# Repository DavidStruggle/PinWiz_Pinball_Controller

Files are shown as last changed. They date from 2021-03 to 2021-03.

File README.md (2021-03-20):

# PinWiz Pinball Controller
 ~ Purpuse Build Open Source Pinball Controller ~ 

## Features
- 10×10 Lamp driver Matrix ( LED and incandescent possible)
- 10×10 Switch matrix
- 40 High Power drivers
- 2.1ch Audio Amplifier  (2x 19W + 1x50W)
- 2ch General Illumination
- 2 Stepper Motor Drivers

## TODO
- Clean up schematics
- Include detailed BOM

## Background
I know that there are other “DIY” Pinball controllers like the PROC or the OPP, but I wanted to do my own (focused on fitting my pinball project). A big difference between my board and these boards is that i am using a central processor for doing everything rather than decentral boards, which do have their own processing unit on them. 

### Extract from my Blog
#### Audio Amplifier

The original game uses stereo music files and mono sound effects (sometimes panned to one speaker).  We also have a woofer in the cabinet, so it would make sense to have a tree way amplifier: two channels for the speakers, one for the woofer. Texas Instruments offers an IC, that fulfills our requirements. The TAS5755M is a very cool and relatively cheap chip. It is controlled by I2C and gets the sound data over standard I2S. I2S is very interesting, since we are basically sending a PCM signal to the codec. PCM is an uncompressed audio format found in wav files, which we are already have from the game files (more on that later). So we just need to read that file and send that exact data over to the codec without decompressing. This saves a lot of CPU load. Mixing multiple files is also easy since we can use simple addition (..and in some cases multiplication/division).

Another Bonus is, that the codec has an internal equalizer, which we can use to get the maximum sound quality out of our cabinet (..and adding a low pass filter to the subwoofer).

##### Stepper Motor Driver

Driving stepper motors is pretty straight forward: All you need are two H-Bridges and you are set (for an bipolar stepper motor). However, this will take some CPU load, handling the PWM signals to the bridges. While investigating, I found an interesting IC. The PCA9629A from NXP can control an uni polar stepper motor (with the help of some external components) over I2C. It has many features like ramping up and down, going x steps, reacting to interrupts and GPIO states. With the help of this IC, we can minimize another load on our processor. I also find it neat to see, that the datasheets states Amusement Machines as the first suggested use case 🙂

#### Solenoid drivers

There is not much to say for this one: The Solenoids will be fired by controlling an IRL540N mosfet in open drain configuration (it pulls the solenoid to ground). The mosfet is driven by a SN74ABT2827 buffer, which has multiple use cases: it is used as an watchdog, disabling all solenoids if the microprocessor has any problem, it is used to safe the microprocessor in case the mosfet fails and it is used as an level translator, since the microprocessor runs at 3.3v and the mosfet likes a gate-source voltage of around 5V.

#### Lamp Matrix drivers

Basically this is a standard TIP102 / TIP107 configuration as you see it on most pinball machines. The TIP102 NPN are buffered with a SN74ABT2827 and the TIP107 PNP are pulled low by ULN2003A darlington arrays. 

#### Switch Matrix drivers
The most simple solution yet: Just In/Out Buffers (SN74ABT2827) controlled by the microcontroller.

#### General Illumination
An IRL540N mosfet driven by a MCP1402 gate driver (used again as level translator). This mosfet will be PWM controlled. 

#### The Microcontroller
The heart of our machine. I have very pleasant experience with the STM32 series of microcontrollers so I stuck with them. The biggest factors here for choosing a microcontroller are:

    Amount of GPIOs
    I2S
    I2C
    SDIO (..at least SPI)
    SPI 

There are quite a few microcontrollers which fulfill our criteria. Luckily, most of them pin compatible. Candidates are : STM32F469 (IE, II or IG) STM32F767 (II or IG), or even STM32H743 (II or IG).

I chose the STM32F767 – it should be more than enough powerful for what we will use it. You could however choose another controller if you like. Porting the source code should not be a problem, since they are all backwards compatible.

#### Miscellaneous

An SD card is directly connected to the microcontroller. The DMD will also be driven directly from the microcontroller. A backup SRAM battery has been added to store variables in SRAM and keep time and date. I probably wont end up using the SRAM for high scores, statistics and options, since its volitale. These things will probably end up in Flash or on the SD (which should be fine, since they are not written all the time). The microcontroller will be programmable over JTAG or SWD. In this case, I have gone with SWD, since it works great on the Nucleo boards.

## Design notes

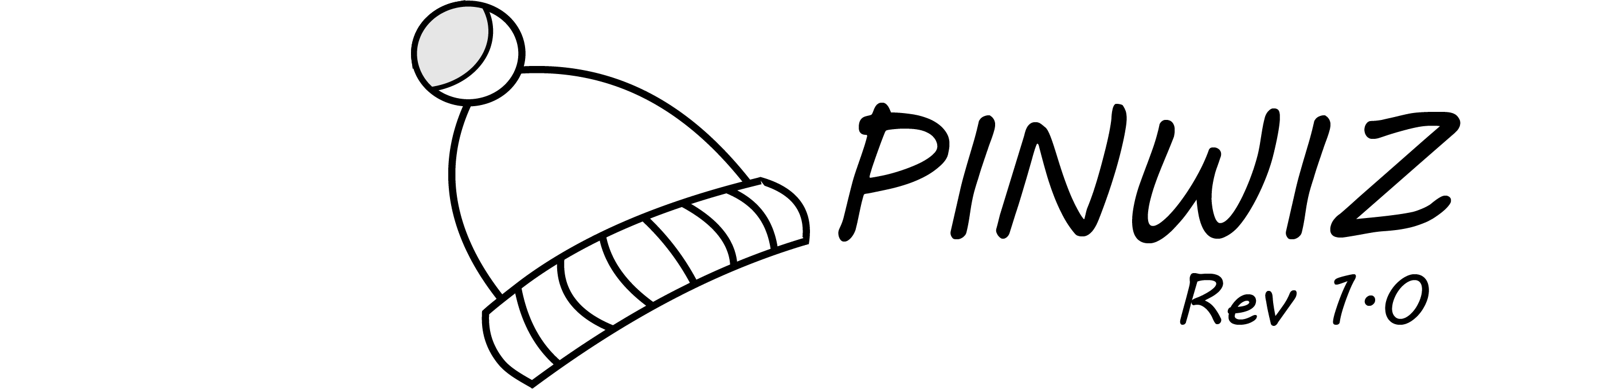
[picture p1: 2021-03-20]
Graphics/PinWiz.png

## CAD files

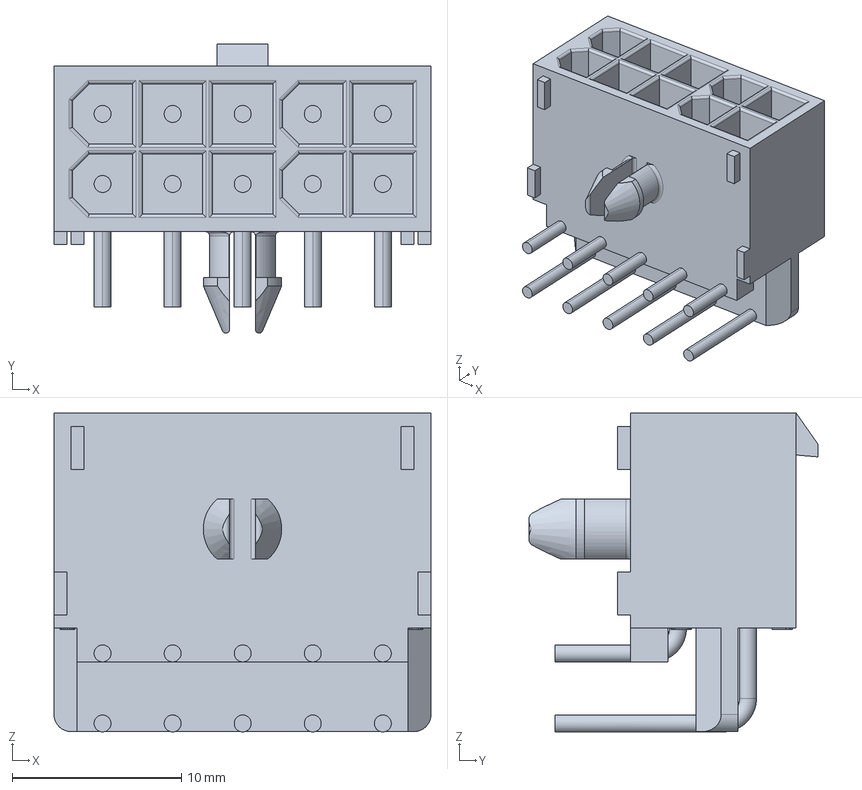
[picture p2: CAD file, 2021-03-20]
Design Files/3D_Modelle/c-770971-1-e-3d.stp
22.3 x 17.1 x 18.8 mm

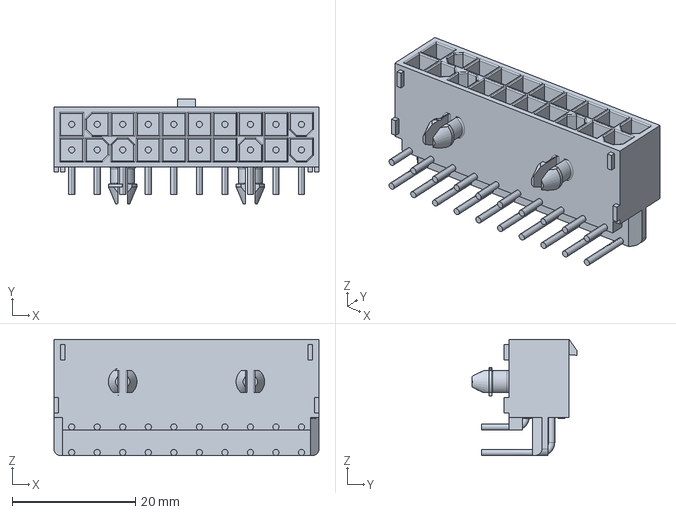
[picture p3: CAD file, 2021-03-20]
Design Files/3D_Modelle/c-794106-2-b-3d.stp
43.0 x 17.1 x 18.8 mm

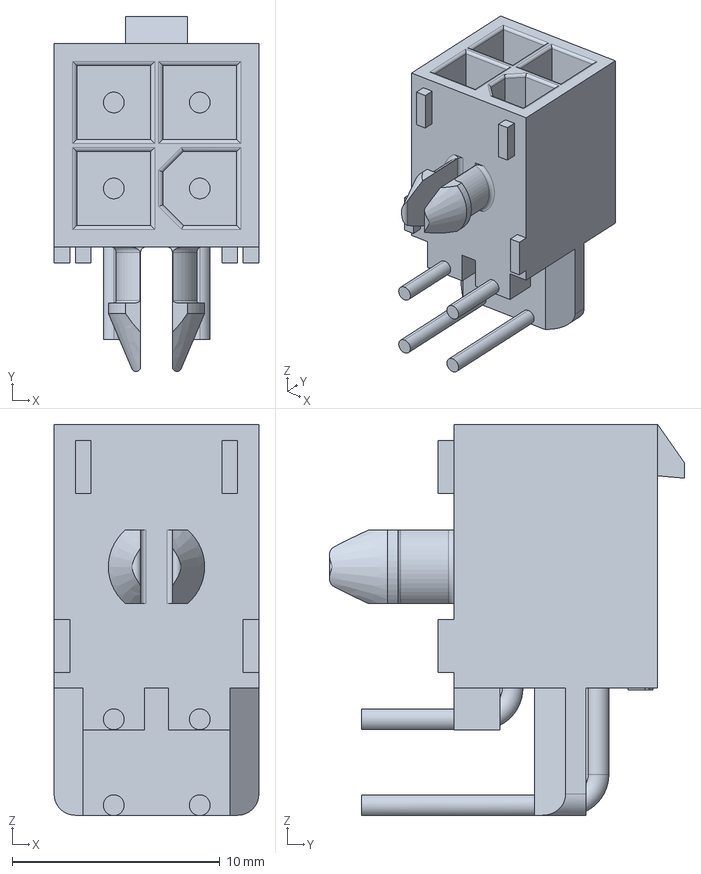
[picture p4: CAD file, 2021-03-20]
Design Files/3D_Modelle/c-1-770968-0-e-3d.stp
9.86 x 17.1 x 18.8 mm

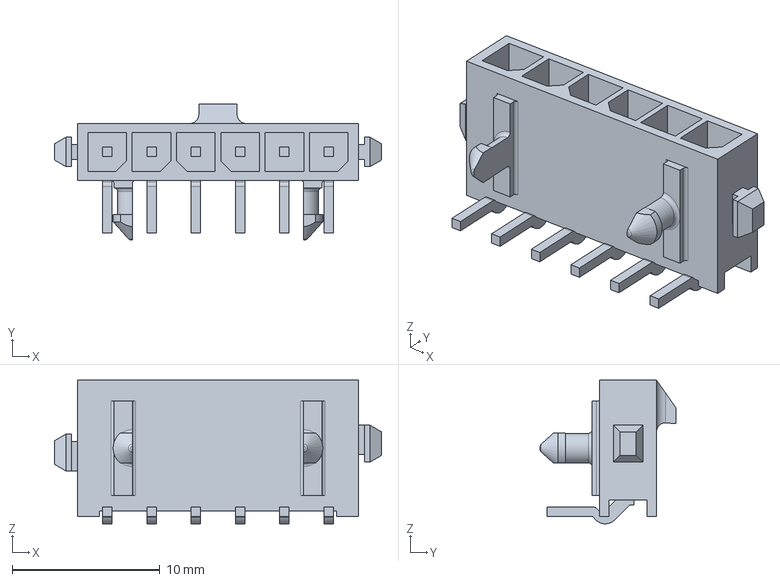
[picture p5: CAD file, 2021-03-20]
Design Files/3D_Modelle/c-1445098-6-b-3d.stp
22.1 x 9.18 x 9.73 mm

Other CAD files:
Graphics/PinWiz.dwg

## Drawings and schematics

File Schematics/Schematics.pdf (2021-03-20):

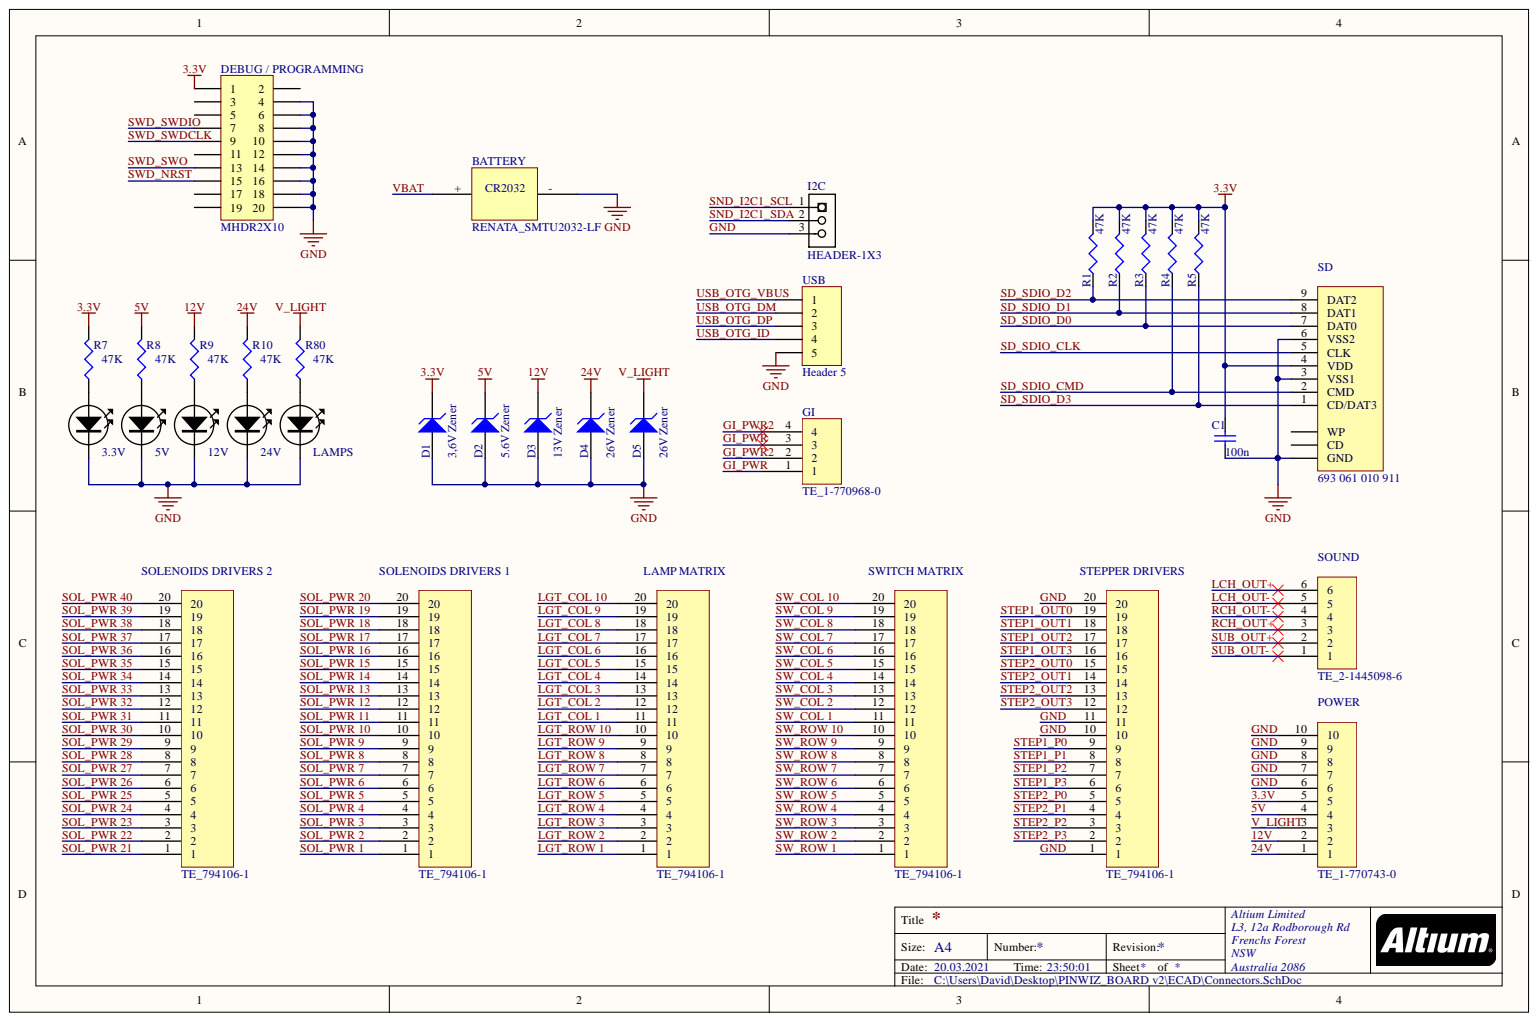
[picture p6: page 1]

* Title | Altium Limited L3, 12a Rodborough Rd Frenchs Forest NSW Australia 2086

A4 Size: | * Number: | * Revision:
Date: 20.03.2021 Time: 23:50:01 | | Sheet * of *

C:\Users\David\Desktop\PINWIZ_BOARD v2\ECAD\Connectors.SchDoc

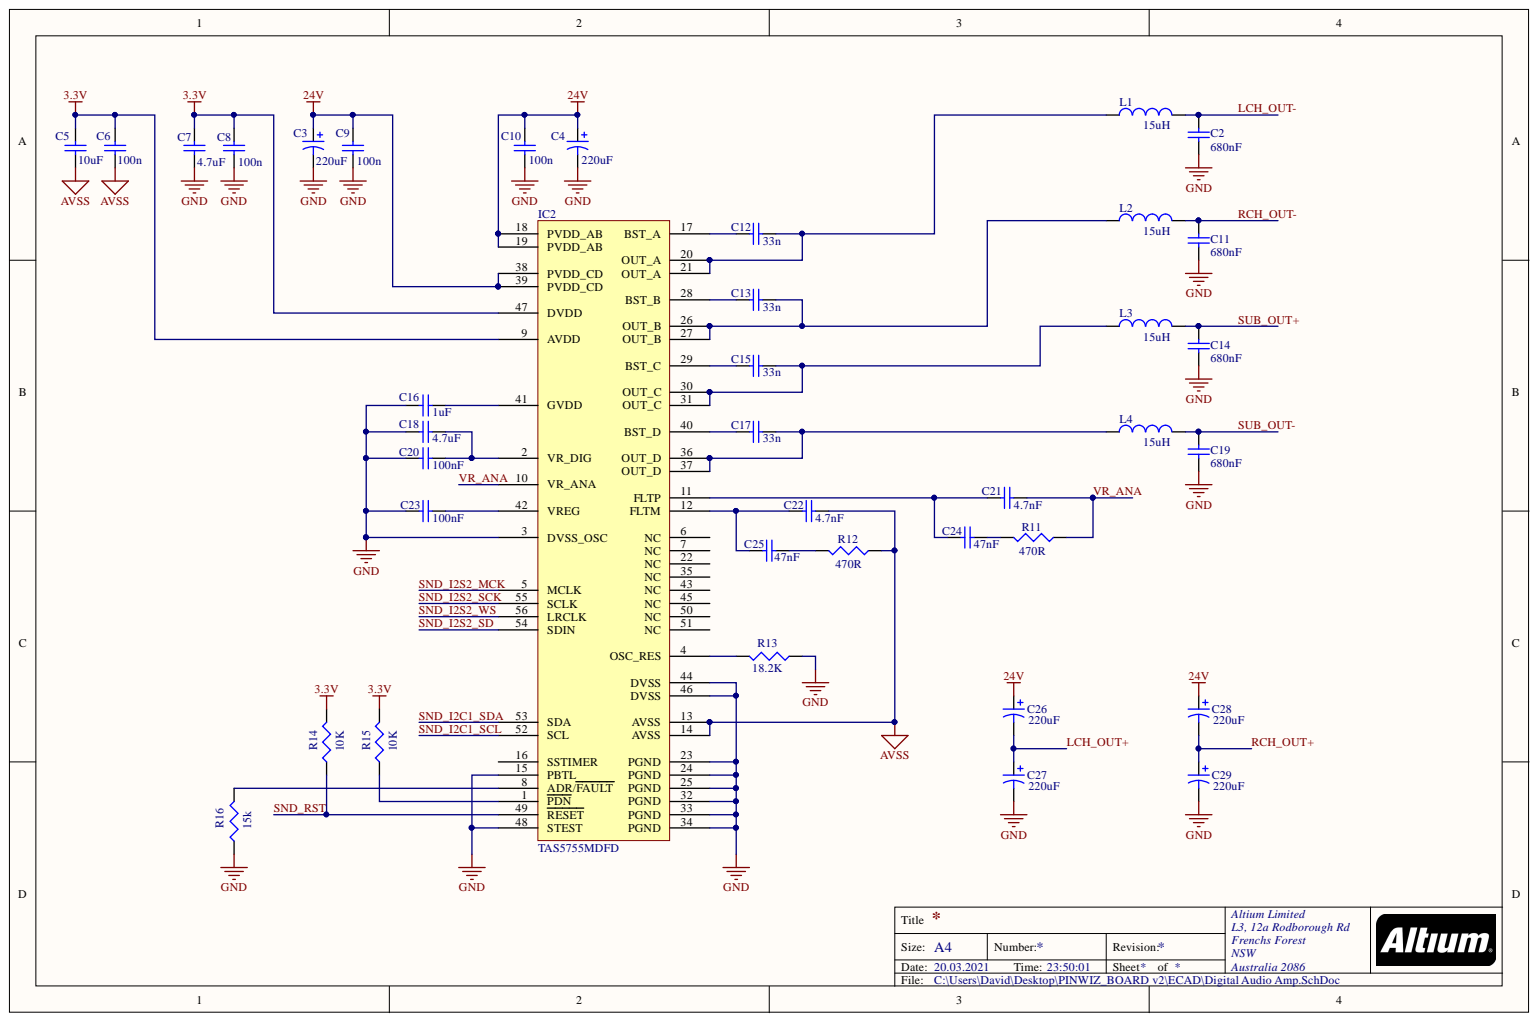
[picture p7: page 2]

8 | | 2 5
1 | | 3 2
4 9 | | 3 3
4 | | 3 4

* T i t l e | A l t i u m Li m i ted L3, 1 2 a R o d b o ro u g h R d F rench s F o res t NS W A u s t r a l i a 2

A4 Size: | * N umber: | * Rev i s i o n :

0.0 3.2 T ime: : : | | Sheet o f

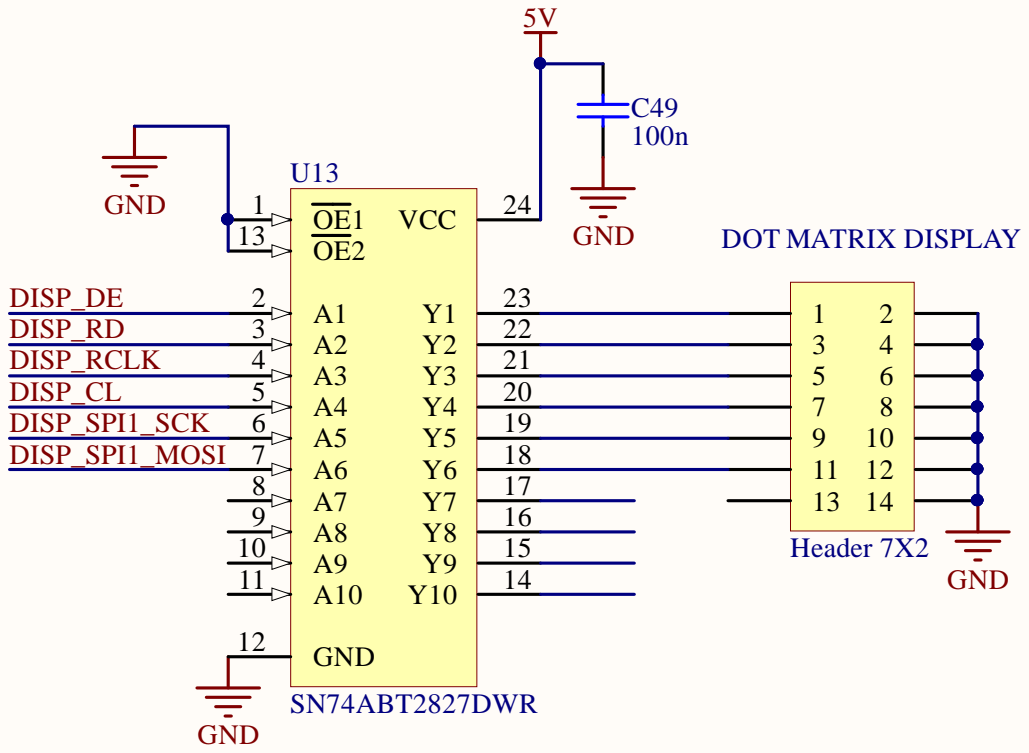
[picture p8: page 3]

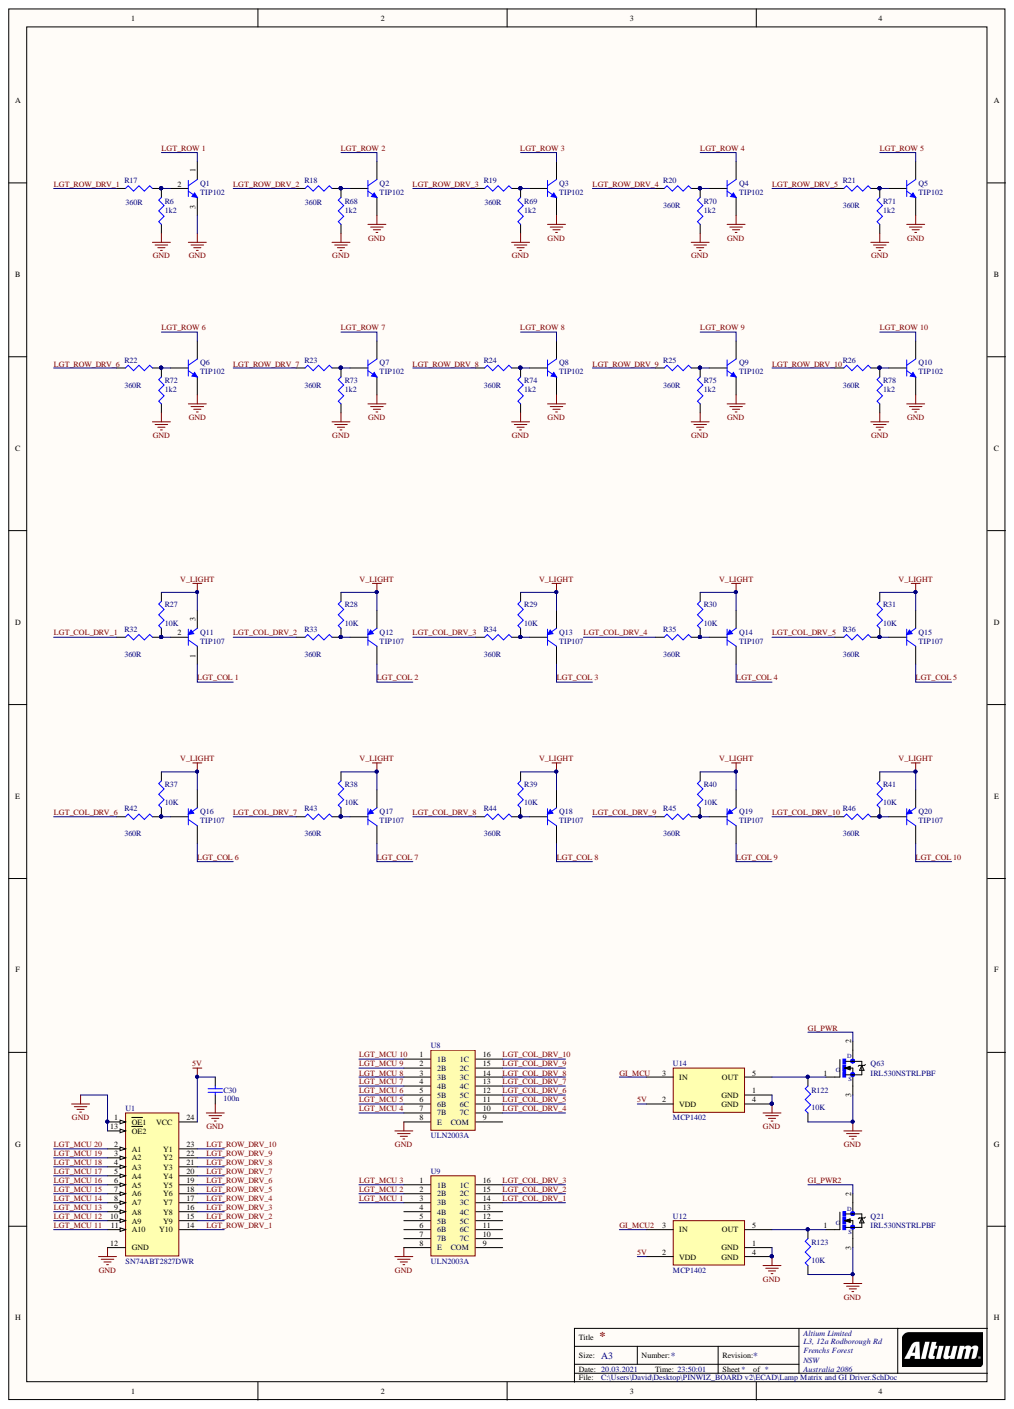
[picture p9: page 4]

Title | Altium Limited L3, 12a Rodborough Rd Frenchs Forest NSW

Size: A3 | Number: * | Revision: *

C:\Users\David\Desktop\PINWIZ_BOARD v2\ECAD\Lamp Matrix and GI Driver.SchDoc

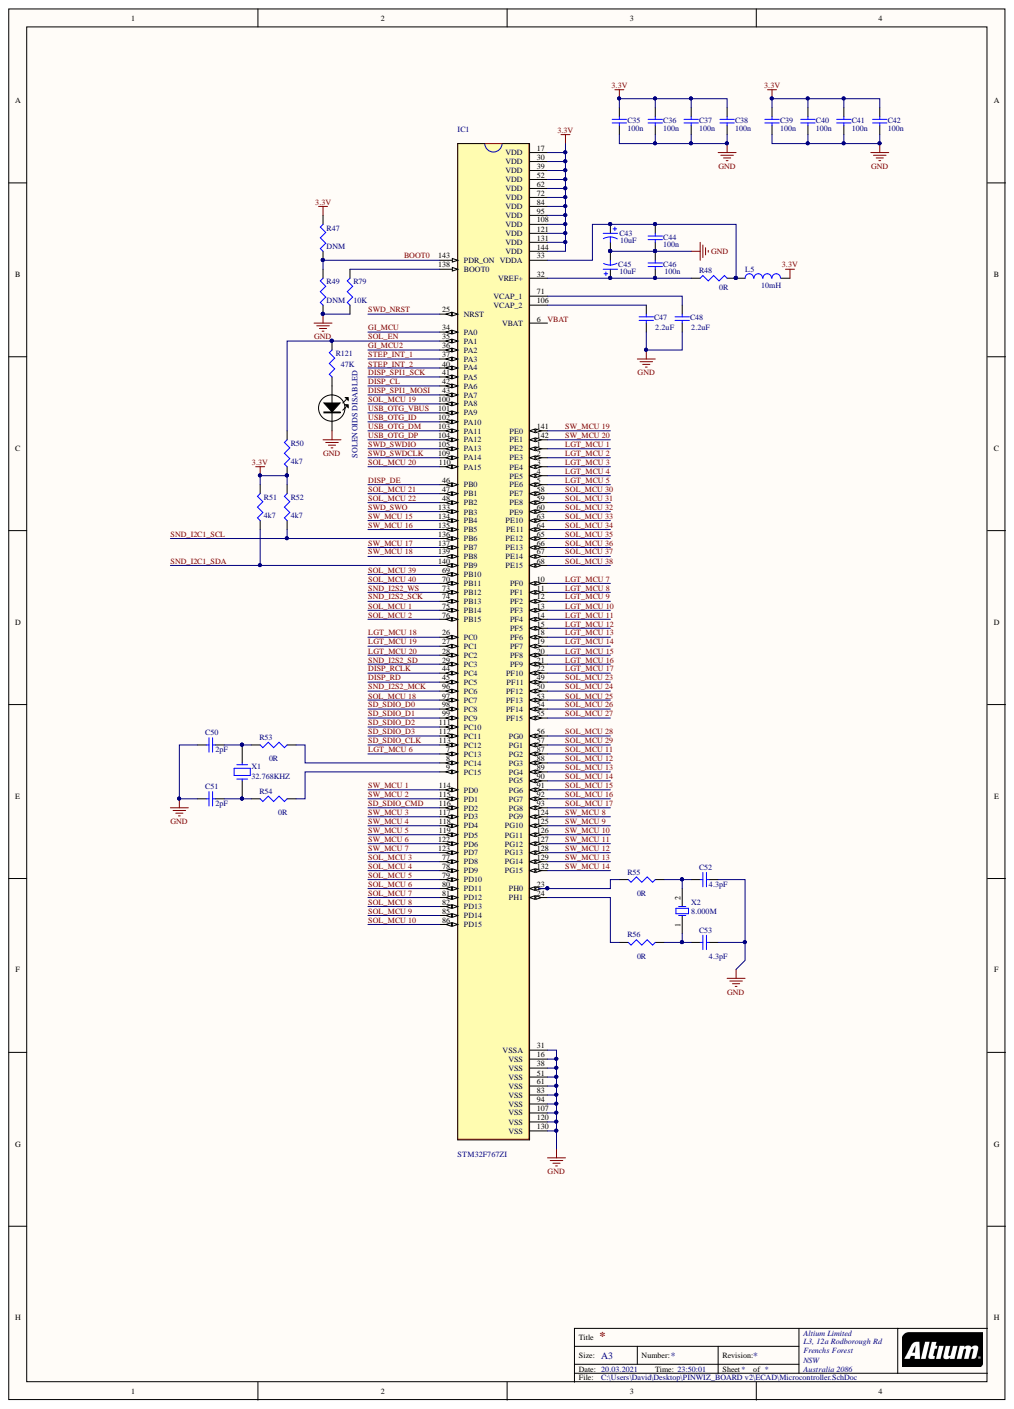
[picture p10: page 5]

Title | Altium Limited L3, 12a Rodborough Rd Frenchs Forest NSW

Size: A3 | Number: * | Revision: *

C:\Users\David\Desktop\PINWIZ_BOARD v2\ECAD\Microcontroller.SchDoc

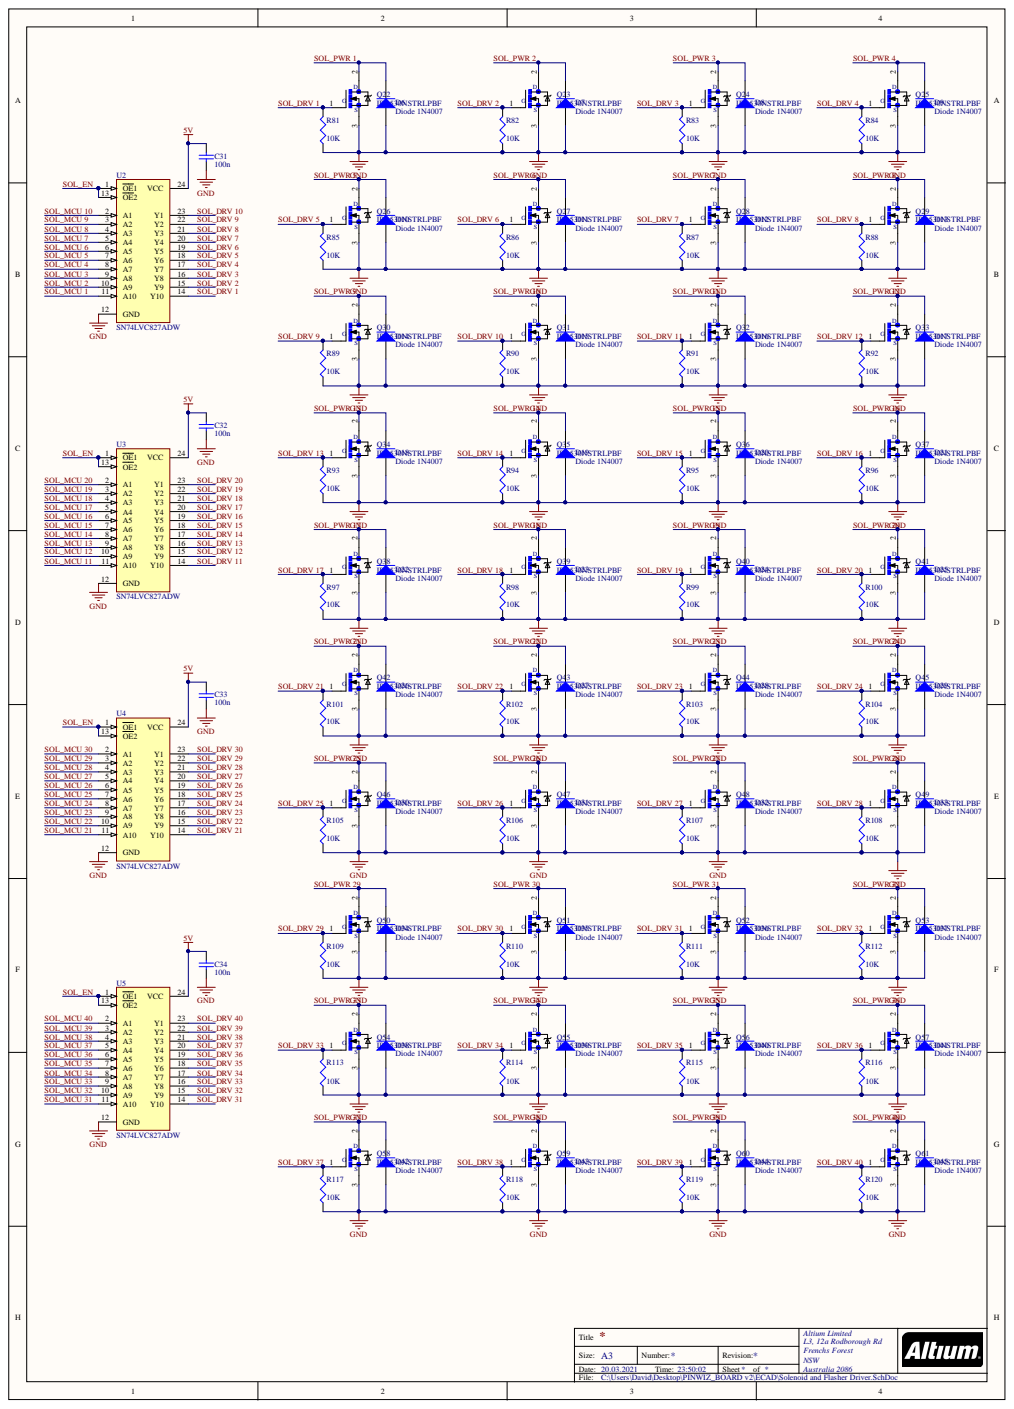
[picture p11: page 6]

Altium Limite d L3, 12a Rodborough R d F renchs Fore s t NSW Australia 2086

A | r : | R evision:

Date : Time : | | She e t of
File : Z_BOARD v2\E CAD\Solenoid and Fla she r Drive r . S chDoc

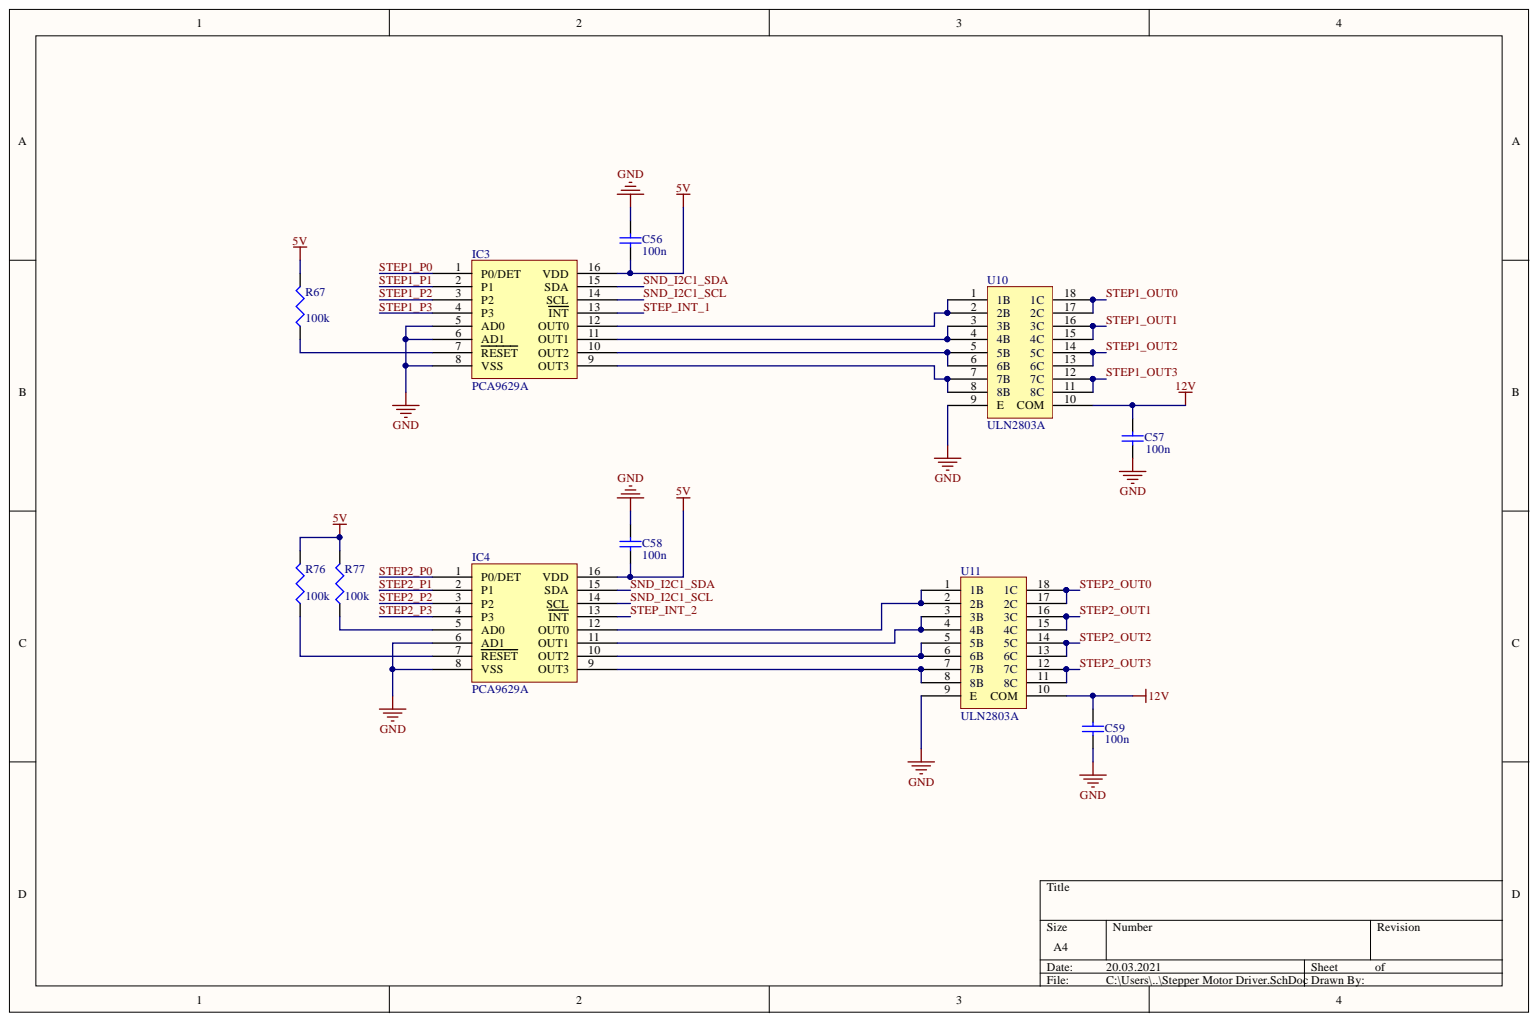
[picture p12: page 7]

6 | | 1 1 | | 4 | 1 5
7 | | 1 0 5

8 | 1 1

6 | | 1 1 | | 5
7 | | 1 0 | | 6 | 1 3

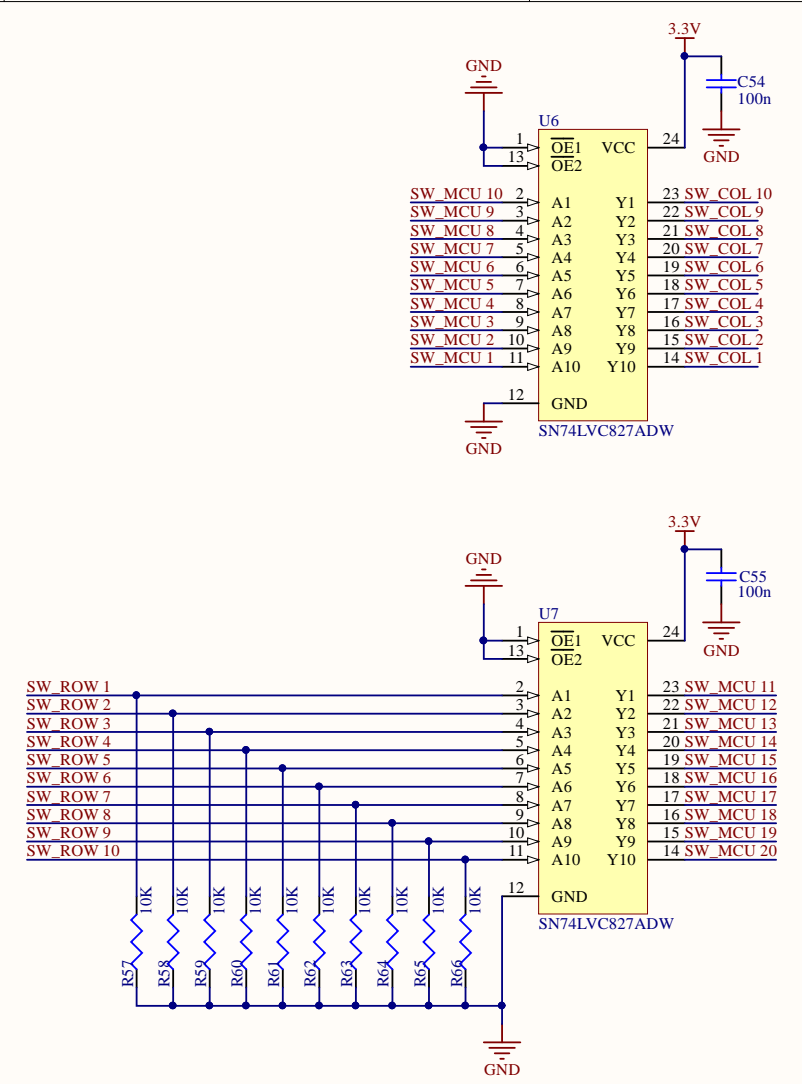
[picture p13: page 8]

* Title | Altium Limited L3, 12a Rodborough Rd Frenchs Forest NSW

A4 Size: | * Number: | * Revision:

C:\Users\David\Desktop\PINWIZ_BOARD v2\ECAD\Switch Matrix Driver.SchDoc

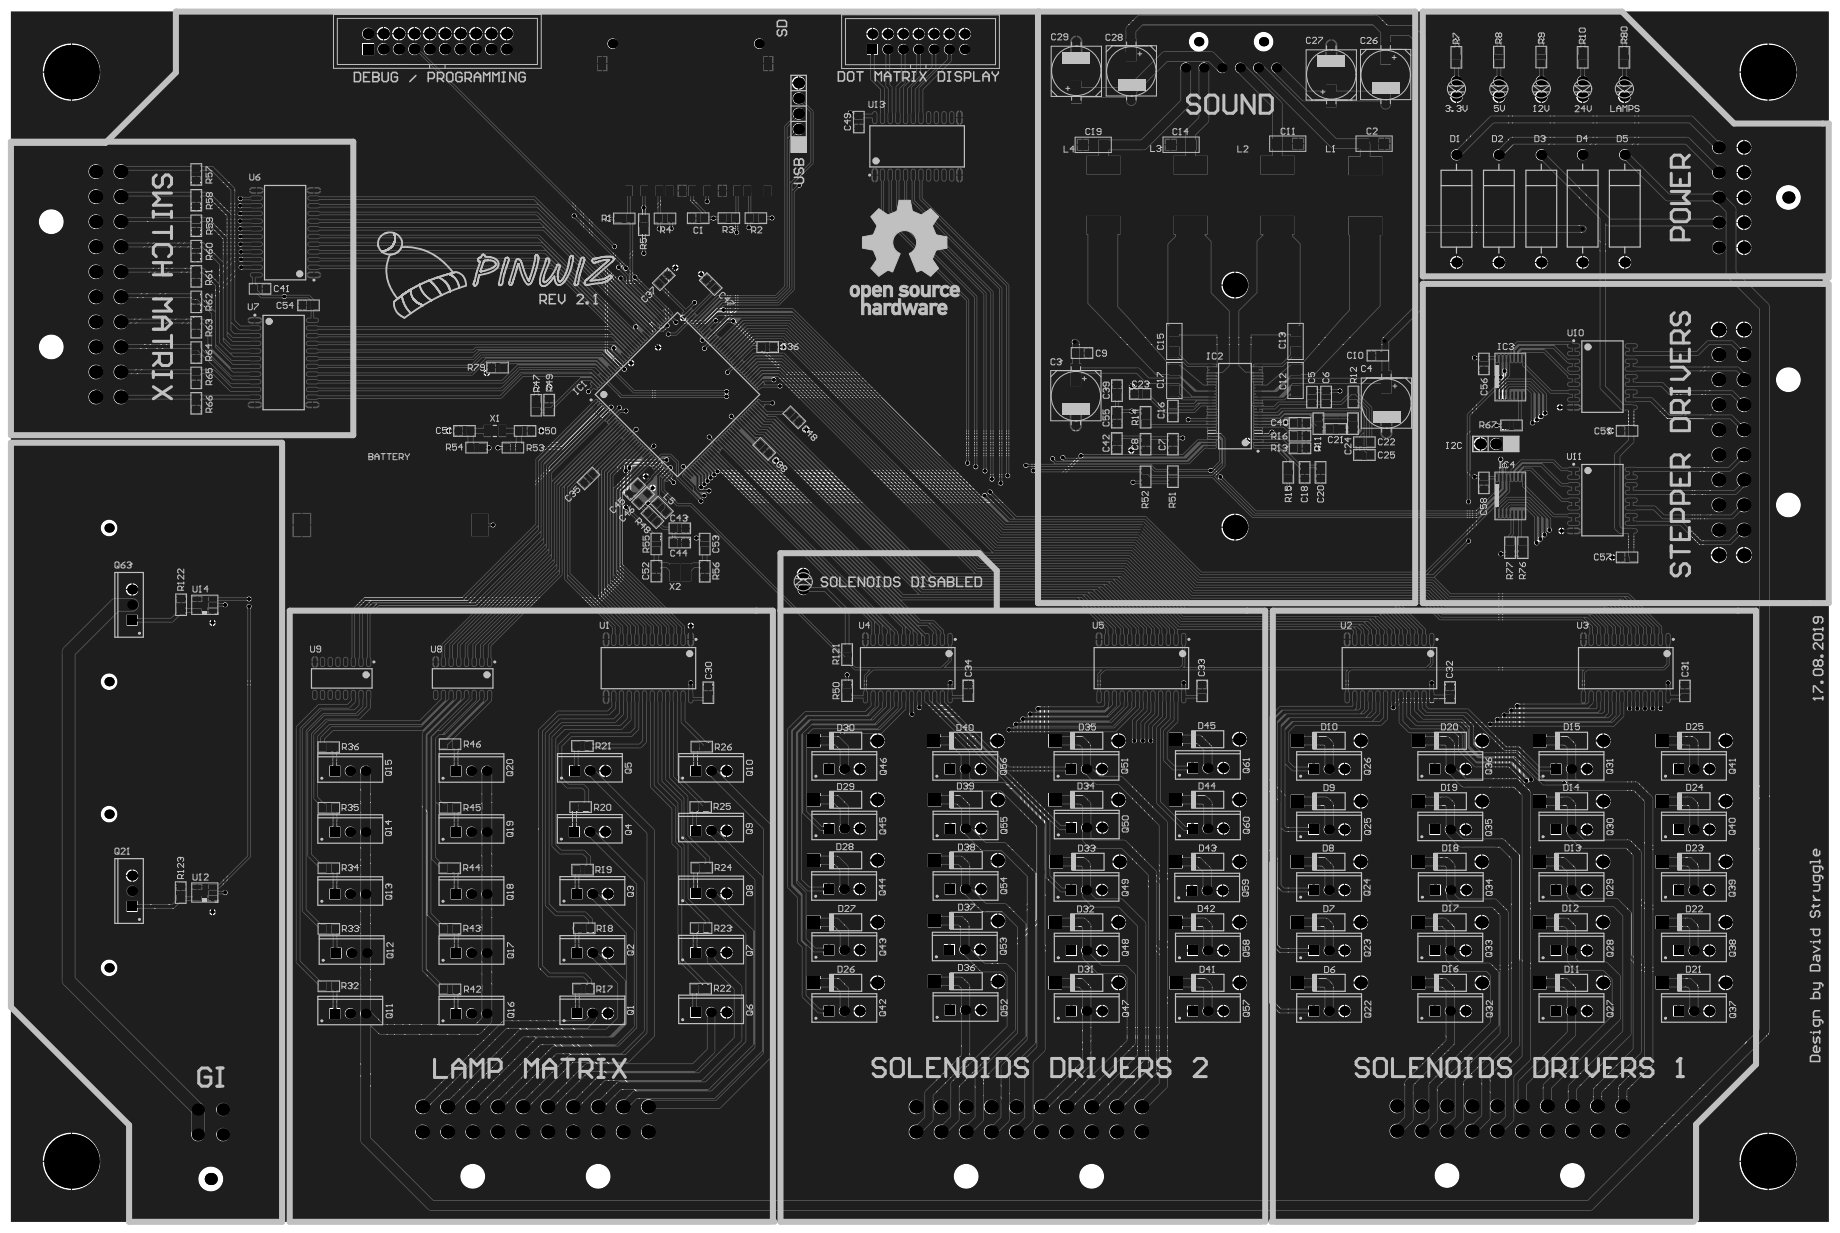
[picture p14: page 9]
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
